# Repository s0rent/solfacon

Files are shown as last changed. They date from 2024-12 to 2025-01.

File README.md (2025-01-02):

# Solfacon
### An efficient fan controller designed for solar powered sustainable / off-grid ventilation

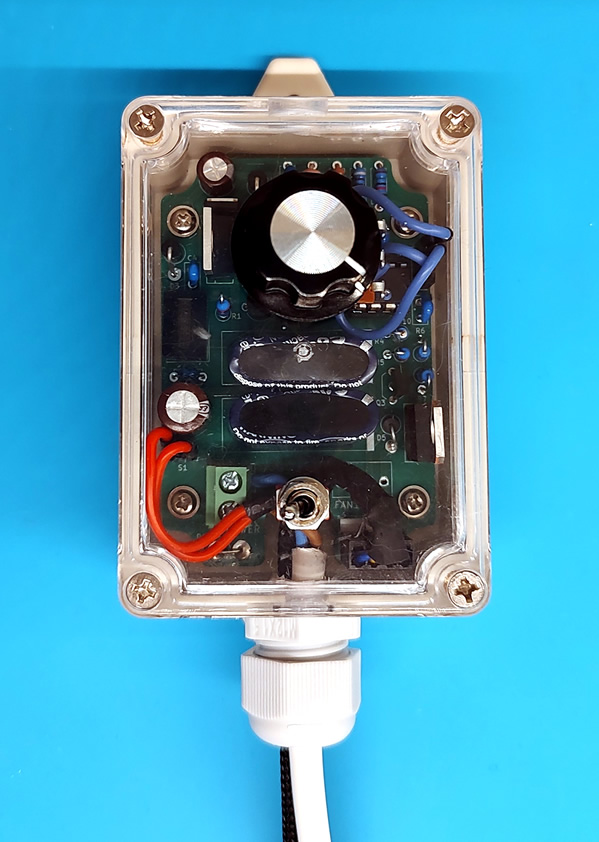
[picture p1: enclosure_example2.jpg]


Feature highlights:
* Low-light operation / assisted fan start
* Adjustable stable fan speed - PWM duty cycle calculated based on available voltage and desired fan speed
* Connect the solar panel and fan(s) directly to the controller (includes fan headers for connecting one or two 3-pin or 4-pin 12V PC fans)
* Configuration tool allows for easy adaptation to any fan make and model (default configuration is for Arctic P12 fans)
* LDO / switch mode combo power regulation for efficient power conditioning - fan operation down to ~4V input voltage
* Easy assembly in standard enclosure with stencil for drilling
* Easy to configure, build, modify and hack

Technical specs:
* Solar panel open circuit voltage: 16V ~ 26V
* Recommended max load: 12W (peak)
* Recommended max total fan power rating: 6W (all fans combined)
* Quiescent current: 5mA
* Operating temperature: -20°C to 50°C
* Fan PWM frequency: 25KHz (Intel PC fan spec)
* MCU: ATtiny85 @ 3.3V

Prerequisites:
* Solar panel
* Fan
* Soldering iron for assembling the controller
* Arduino IDE for flashing the MCU
* ISP for flashing the MCU

Read more here and configure your own using the configuration tool:
https://s0rent.github.io/solfacon/

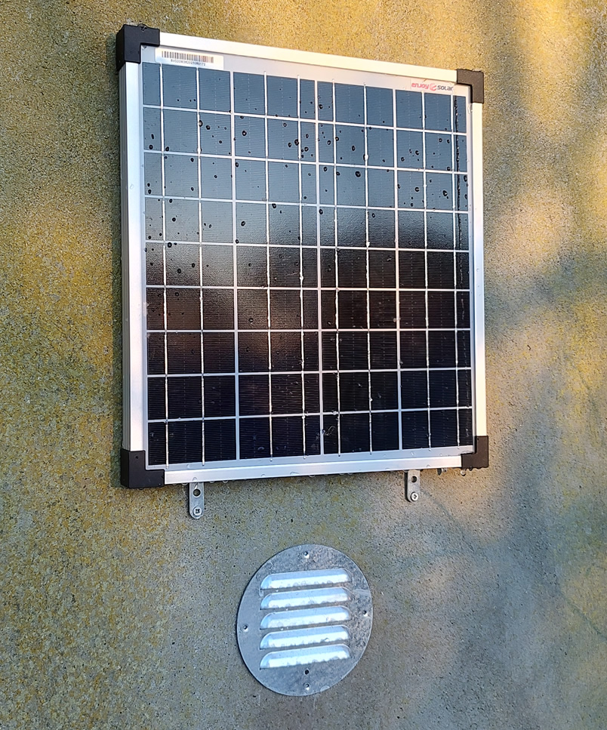
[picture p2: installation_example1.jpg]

"Low-light operation / assisted fan start" allows fan start and operation in otherwise difficult conditions, such as partial shade, suboptimal panel angle and at dawn/dusk. The photo above is a setup with a 20W panel and one fan (Arctic P12), and the fan is running continuously despite the panel only being partially exposed to faint sunlight right after dawn. In this situation the panel only supplies around 20mA, but the controller design allows it to buffer enough energy to efficiently start the fan and keep it running.

Software used: <br>
* KiCad 6.0
* Arduino IDE 2.2.0 (should be compatible with newer versions as well)
* ATtiny package for Arduino IDE (https://github.com/damellis/attiny)

Hardware used: <br>
* USBtinyISP (it is also possible to use for instance an Arduino as ISP)

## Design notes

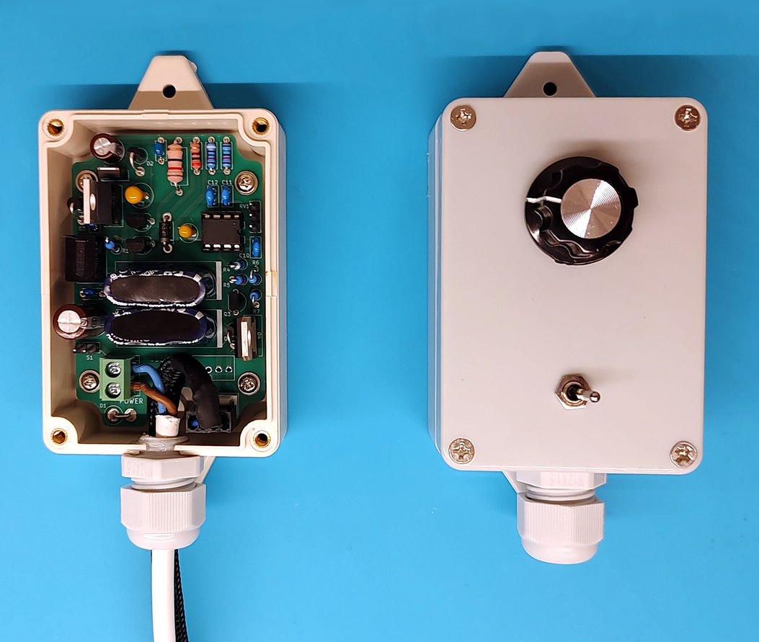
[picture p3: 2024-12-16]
enclosure_example1.jpg

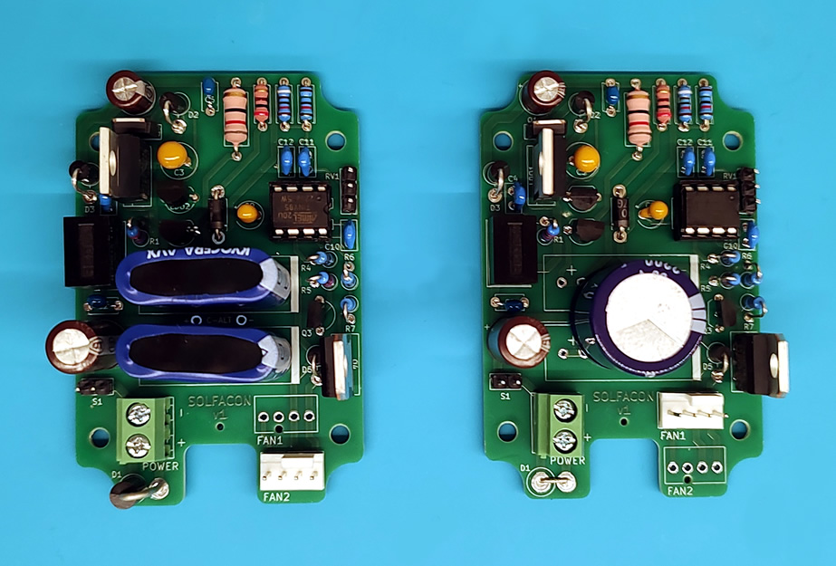
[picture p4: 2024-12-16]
pcb_examples.jpg

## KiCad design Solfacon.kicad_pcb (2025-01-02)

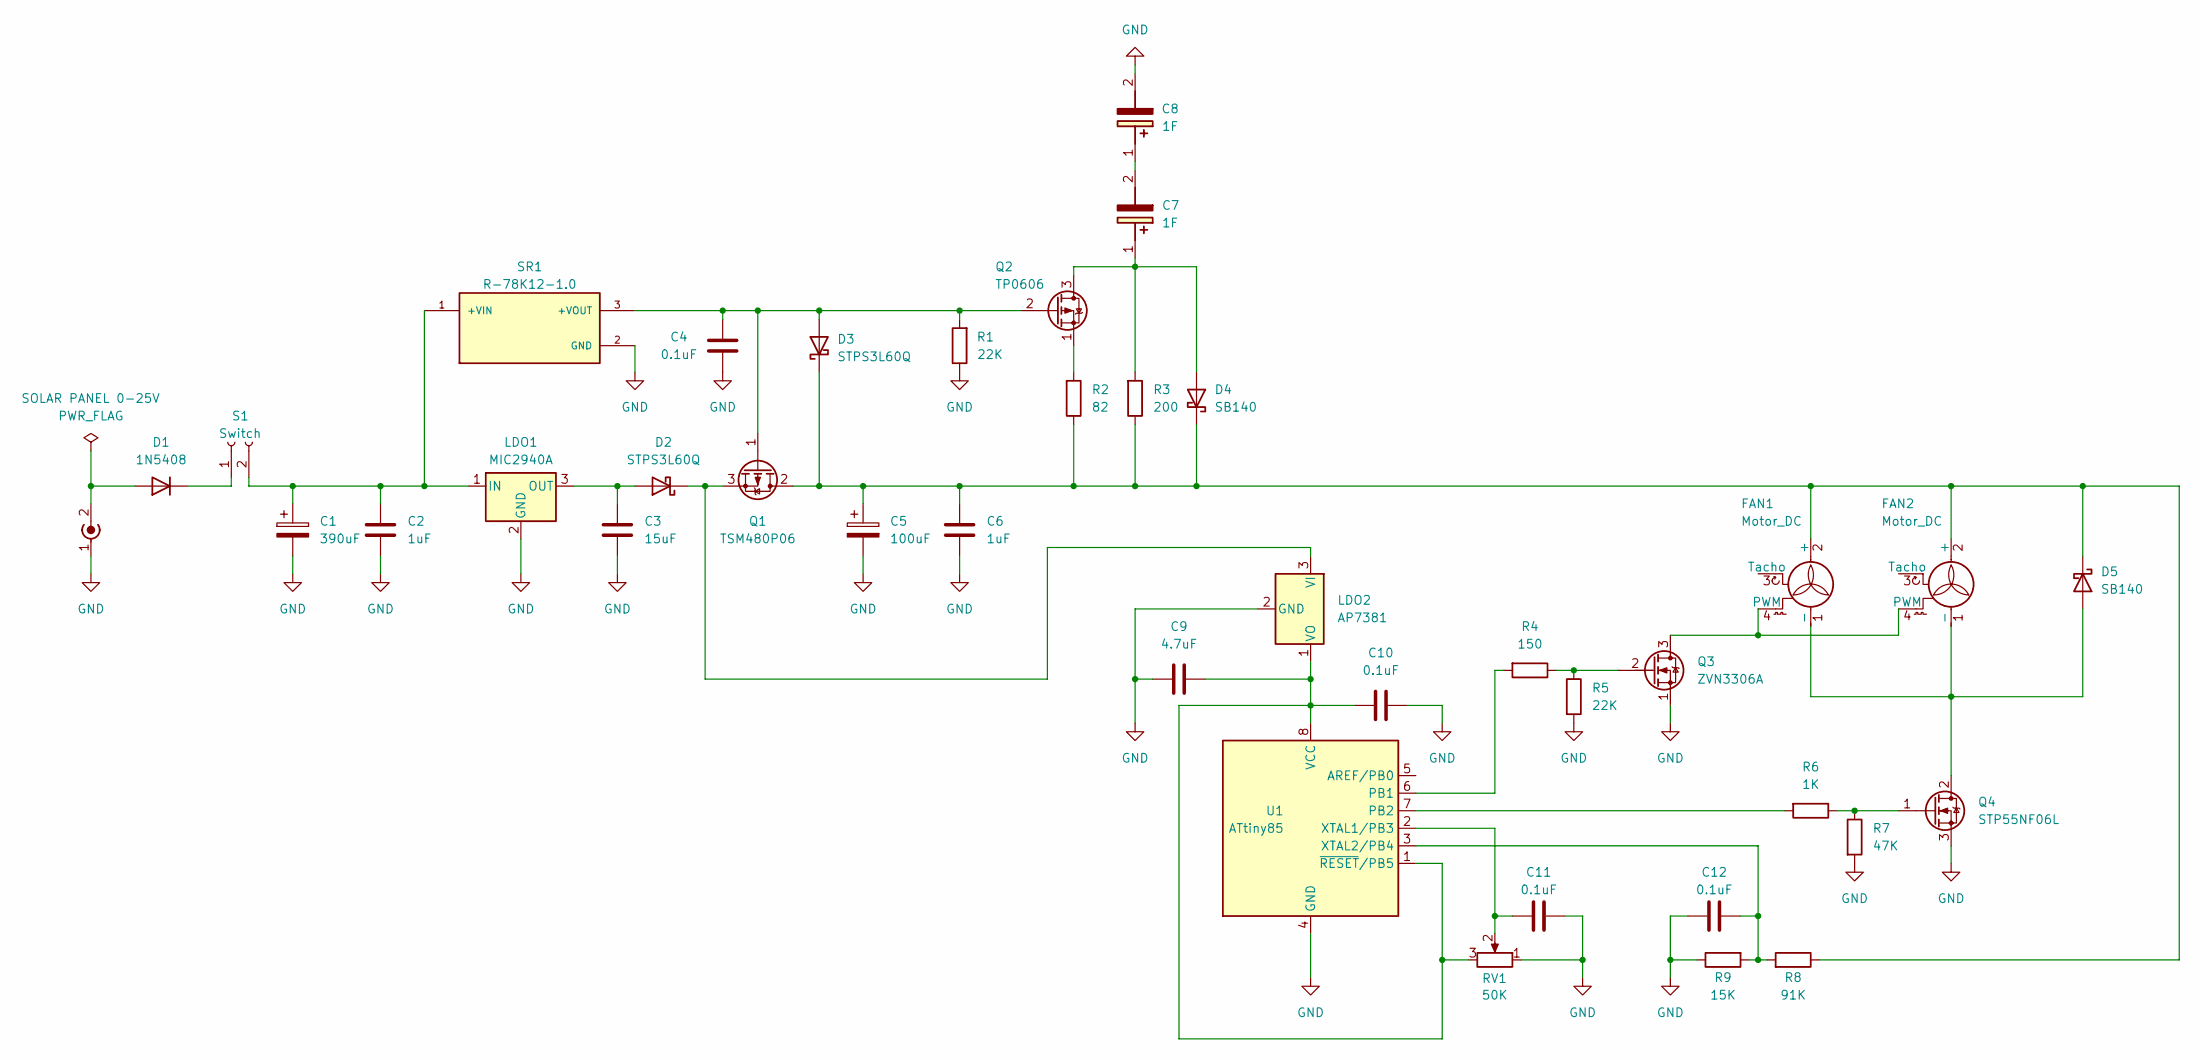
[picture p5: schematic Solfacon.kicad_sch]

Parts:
C1: 390uF; CP_Radial_D8.0mm_P3.50mm
C2, C6: 1uF; C_Disc_D4.7mm_W2.5mm_P5.00mm
C3: 15uF; CP_Radial_Tantal_D6.0mm_P2.50mm
C4, C10, C11, C12: 0.1uF; C_Disc_D5.0mm_W2.5mm_P2.50mm
C5: 100uF; CP_Radial_D6.3mm_P2.50mm
C7, C8: 1F; SCMR14L334SSBB0
C9: 4.7uF; CP_Radial_Tantal_D4.5mm_P2.50mm
D1: 1N5408; D_DO-201AD_P4.00mm_Vertical_AnodeUp
D2, D3: STPS3L60Q; D_DO-15_P3.81mm_Vertical_AnodeUp
D4: SB140; D_DO-41_SOD81_P7.62mm_Horizontal
D5: SB140; D_DO-41_SOD81_P3.81mm_Vertical_AnodeUp
FAN1, FAN2: Motor_DC; CONN_SD-47053-001_H10p00_MOL
LDO1: MIC2940A; TO-220-3_Vertical
LDO2: AP7381; TO-92_Inline_Wide
POWER1: SOLAR PANEL 0-25V; TerminalBlock_RND_205-00045_1x02_P5.00mm_Horizontal
Q1: TSM480P06; TO-251-3_Vertical
Q2: TP0606; TO-92_Inline_Wide
Q3: ZVN3306A; TO-92_Inline_Wide
Q4: STP55NF06L; TO-220-3_Vertical
R1, R5: 22K; R_Axial_DIN0207_L6.3mm_D2.5mm_P2.54mm_Vertical
R2: 82; R_Axial_DIN0309_L9.0mm_D3.9mm_P12.70mm_Horizontal
R3: 200; R_Axial_DIN0207_L6.3mm_D2.5mm_P7.62mm_Horizontal
R4: 150; R_Axial_DIN0207_L6.3mm_D2.5mm_P2.54mm_Vertical
R6: 1K; R_Axial_DIN0207_L6.3mm_D2.5mm_P2.54mm_Vertical
R7: 47K; R_Axial_DIN0207_L6.3mm_D2.5mm_P2.54mm_Vertical
R8: 91K; R_Axial_DIN0207_L6.3mm_D2.5mm_P7.62mm_Horizontal
R9: 15K; R_Axial_DIN0207_L6.3mm_D2.5mm_P7.62mm_Horizontal
RV1: 50K; PinHeader_1x03_P2.54mm_Vertical
S1: Conn_01x02_Female; PinHeader_1x02_P2.54mm_Vertical
SR1: R-78K12-1.0; CONV_R-78K12-1.0; PARTREV 0/2023
U1: ATtiny85; DIP-8_W7.62mm

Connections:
unnamed: C1.1, C2.1, LDO1.1 (IN), S1.2, SR1.1 (+VIN)
unnamed: C3.1, D2.2 (A), LDO1.3 (OUT)
unnamed: C4.1, D3.2 (A), Q1.1 (G), Q2.2 (G), R1.2, SR1.3 (+VOUT)
unnamed: C5.1, C6.1, D3.1 (K), D4.1 (K), D5.1 (K), FAN1.2 (+), FAN2.2 (+), Q1.2 (D), R2.1, R3.1, R8.1
unnamed: C7.1 (+), D4.2 (A), Q2.3 (D), R3.2
unnamed: C7.2 (-), C8.1 (+)
unnamed: C9.2, C10.2, LDO2.1 (VO), RV1.3, U1.1 (~RESET/PB5), U1.8 (VCC)
unnamed: C11.1, RV1.2, U1.2 (XTAL1/PB3)
unnamed: C12.1, R8.2, R9.2, U1.3 (XTAL2/PB4)
unnamed: D1.1 (K), S1.1
unnamed: D1.2 (A), POWER1.2 (In)
unnamed: D2.1 (K), LDO2.3 (VI), Q1.3 (S)
unnamed: D5.2 (A), FAN1.1 (-), FAN2.1 (-), Q4.2 (D)
unnamed: FAN1.4 (PWM), FAN2.4 (PWM), Q3.3 (D)
unnamed: Q2.1 (S), R2.2
unnamed: Q3.2 (G), R4.1, R5.1
unnamed: Q4.1 (G), R6.1, R7.1
unnamed: R4.2, U1.6 (PB1)
unnamed: R6.2, U1.7 (PB2)

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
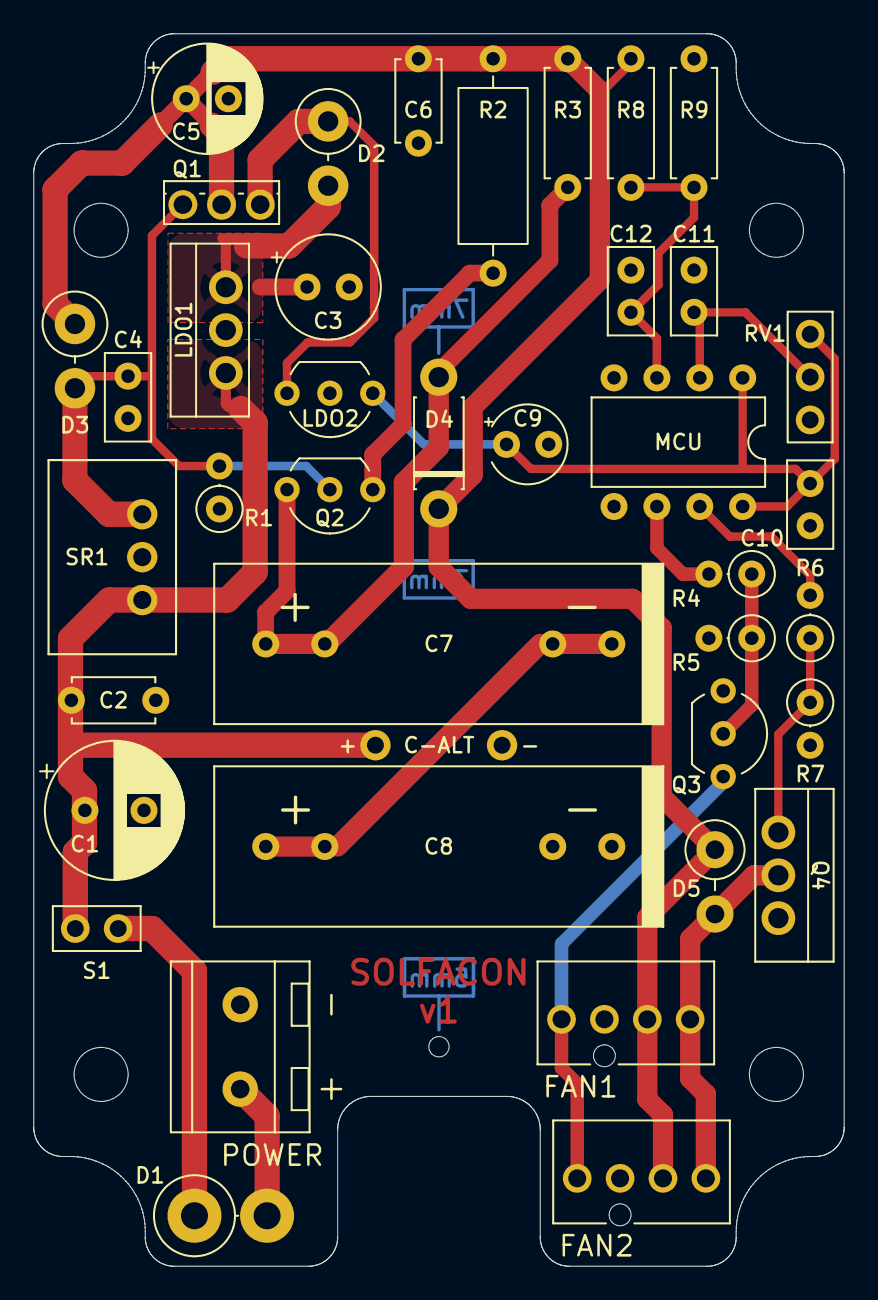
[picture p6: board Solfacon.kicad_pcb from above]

Board: 2 copper layers, 48.0 x 73.0 mm, 40 parts (0 on the bottom side), 20 nets.

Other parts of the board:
 : MountingHole_2mm

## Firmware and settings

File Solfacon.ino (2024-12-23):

#include "util/delay.h"  // Any delays used are off by factor ~1.3 due to interrupts caused by timer0 (PWM out) - only matters if you need exact timing
#include "fan-curve.h"

#define F_CPU 800000

/*
Physical pin numbers:
[5] : OUT fan on/off (for LED?)
[6] : OUT pwm
[7] : OUT fan on/off (high/low) 
[2] : IN  max fan speed potentiometer 1/2 -> 1/1
[3] : IN  12V rail voltage divider
*/

#define pinOutLED PB0
#define pinOutPWM PB1
#define pinOutFanEnable PB2
#define pinInTargetFanSpeed MUX3
#define pinInVoltage12VRail MUX2

const byte speedAdjustmentEnabled = true;
const byte lowPowerOperationEnabled = true;
const byte adaptiveModeEnabled = true;  // Usable when speed adjustment is not enabled or target speed = max speed.

const byte measurementsPerSecond = 64;
const byte delayBetweenMeasurements = 1000 / measurementsPerSecond;
// variables for averaging voltages in a 1/4 second window
byte latestVoltageMeasurements[16] = { 0, 0, 0, 0, 0, 0, 0, 0, 0, 0, 0, 0, 0, 0, 0, 0 };
byte voltageMeasurementIndex = 0;

bool fanOn = false;
byte fanTargetSpeed = 63;  // Target speed relative to max speed - range 0-63 (40%-88%)
byte voltage12VRail = 0;   // Voltage relative to max voltage - range 0-127
byte dutyCycle = 40;

void setup() {
  pinMode(pinOutLED, OUTPUT);
  digitalWrite(pinOutLED, LOW);

  pinMode(pinOutPWM, OUTPUT);
  pinMode(pinOutFanEnable, OUTPUT);

  digitalWrite(pinOutPWM, LOW);
  digitalWrite(pinOutFanEnable, LOW);

  cli();

  // ADC config
  ADMUX = 0 << REFS1 | 0 << REFS0;
  ADCSRA = _BV(ADEN) | _BV(ADPS2) | _BV(ADPS1);

  // Timer0 configured for phase correct PWM at 25KHz
  // Since the PWM signal from the MCU controls a MOSFET that pulls the PWM pin of the fan low when the MCU pin is high, the PWM signal is inverted.
  TCCR0A = _BV(COM0B1) | _BV(COM0B0) | _BV(WGM00);
  TCCR0B = _BV(WGM02) | _BV(CS00);
  OCR0A = 160;
  setDutyCycle(160);

  sei();
  _delay_ms(1);
}

void loop() {
  measure12vRailVoltage();
  if (fanOn) {
    measureFanTargetSpeed();
    setDutyCycle(getOptimalDutyCycle());
  }
  _delay_ms(delayBetweenMeasurements);
}

void measure12vRailVoltage() {
  byte adcReading = readADC_8bit(pinInVoltage12VRail);
  voltage12VRail = adcReading - (adcReading >> 5);  // ADC readings of the voltage divider top out at ~131 for 12V, so it must be scaled down to top at 127

  if (voltage12VRail > 127) voltage12VRail = 127;  // The voltage regulators, diodes, and resistors have some margin of error which means that the measured voltage could be 12V or above

  voltageMeasurementIndex++;
  if (voltageMeasurementIndex > 15) voltageMeasurementIndex = 0;
  latestVoltageMeasurements[voltageMeasurementIndex] = voltage12VRail;

  if (voltage12VRail >= fanOnVoltageThreshold && !fanOn) {
    // Voltage is high and the fan is off -> start the fan
    enableFan();
  } else if (voltage12VRail <= fanOffVoltageThreshold && fanOn) {
    // Voltage is low and the fan is on -> stop the fan
    disableFan();
  }
}

void measureFanTargetSpeed() {
  if (!speedAdjustmentEnabled) return 63;

  byte adcReading = readADC_8bit(pinInTargetFanSpeed);
  fanTargetSpeed = adcReading >> 2;  // ADC readings of 0-255 are scaled down to 0-63

  // The ability to reach max on a potentiometer depends on the potentiometer mechanics which can be imperfect. Some cannot reach it, others reach it before the end of the turn.
  // To ensure that the highest speed is reachable, we add a little margin.
  if (fanTargetSpeed > 61) fanTargetSpeed = 63;
}

void enableFan() {
  if (lowPowerOperationEnabled) {
    _delay_ms(10000);  // Wait a bit to increase the likelihood of a good charge
  } else {
    _delay_ms(1000);
  }
  digitalWrite(pinOutLED, HIGH);
  fanOn = true;
  digitalWrite(pinOutFanEnable, HIGH);
  setDutyCycle(32);  // using 20% duty cycle - Less than the full 100% in order to minimize the surge, but enough to ensure that the fan can start.
  _delay_ms(1500);

  if (!lowPowerOperationEnabled) {
    // Without the super capacitors the voltage can drop significantly, but "freewheeling" briefly can make it recover (or at least decrease the risk of brown out) and allow normal operation
    setDutyCycle(160);
    _delay_us(10);
    digitalWrite(pinOutLED, LOW);
    digitalWrite(pinOutFanEnable, LOW);
    _delay_ms(800);
    digitalWrite(pinOutLED, HIGH);
    digitalWrite(pinOutFanEnable, HIGH);
    setDutyCycle(32);
    _delay_ms(800);
  } else {
    _delay_ms(1000);
  }
}

void disableFan() {
  digitalWrite(pinOutLED, LOW);
  fanOn = false;
  setDutyCycle(160);                   // In inverted PWM, the PWM output is now pulled low and the MOSFET is off.
  _delay_us(10);                       // Wait so that the gate of the MOSFET controlling PWM is no longer charged, and there is no connection to GND from the fan's internal pull-up resistor
  digitalWrite(pinOutFanEnable, LOW);  // Now the fan has no path to GND
  _delay_ms(4000);                     // Wait before starting over
}

void setDutyCycle(byte newDutyCycle) {
  OCR0B = newDutyCycle;
}

byte getOptimalDutyCycle() {
  if (adaptiveModeEnabled && fanTargetSpeed == 63) {
    // Max speed setting
    // There is no way to reach max speed at less than full voltage, so there is no ramp up/down noise concern here
    // Instead, we enter "Adaptive mode" where we try to adjust the duty cycle to maintain operation above fanOnVoltageThreshold, since lower duty cycle is more efficient than letting the voltage drop
    // Fan speed might fluctuate wildly, but it there is a bigger chance that the fan will keep running, and it will run as fast as possible
    if (voltage12VRail > fanOnVoltageThreshold) {
      if (getlatestVoltageMeasurementsAverage() > voltage12VRail) {  // below average
        decreseDutyCycle();
      } else {  // above or equal to average
        increaseDutyCycle();
      }
    } else {
      decreseDutyCycle();
    }
  } else if (voltage12VRail >= minimumVoltageForPWM) {
    // Fixed max speed
    // Try to maintain the speed no matter the circumstances
    dutyCycle = pgm_read_byte(&dutyCycleTable[voltage12VRail - minimumVoltageForPWM][fanTargetSpeed]);
  } else {
    dutyCycle = 160;  // default to max duty cycle = PWM off
  }
  return dutyCycle;
}

byte getlatestVoltageMeasurementsAverage() {
  int average = 0;
  for (byte i = 0; i < 16; i++) {
    average += latestVoltageMeasurements[i];
  }
  return average >> 4;
}

void increaseDutyCycle() {
  if (dutyCycle < 160) {
    dutyCycle++;
  }
}

void decreseDutyCycle() {
  byte minimumDutyCycleAtVoltage = pgm_read_byte(&minimumDutyCycle[voltage12VRail - fanOffVoltageThreshold]);
  if (dutyCycle > minimumDutyCycleAtVoltage) {
    dutyCycle-=2;
  } else {
    dutyCycle = minimumDutyCycleAtVoltage;
  }
}

byte readADC_8bit(byte ADmuxPin) {
  // Disables interrupts (and PWM) to give the ADC some quiet time to do its thing.
  // Leaves the PWM output hanging in which ever state it is in.
  cli();
  ADMUX = (ADMUX & 0xF0) + ADmuxPin;
  _delay_us(10);
  ADCSRA |= 1 << ADSC;
  while (ADCSRA & _BV(ADSC));
  sei();
  return (ADC >> 2) & 0xFF;
}
